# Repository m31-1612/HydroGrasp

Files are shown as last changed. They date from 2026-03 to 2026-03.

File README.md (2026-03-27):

# HydroGrasp

This is the official open-source repository for the paper:

**HydroGrasp: A Hydraulic Multi-Fingered Gripper**

📄 [Read the Paper](https://doi.org/10.1109/robio66223.2025.11377340)

---

## Hardware

### Manipulator

To manufacture a manipulator, you need to 3D print the following models in `CAD/Manipulator`. It is recommend to use resin (SLA) 3D printing to achieve better structural accuracy.

#### 3D Printing BOM

| Item | Quantity | Recommand Process|
|---|---|---|
|Base|1|SLA|
|EndNut|6|SLA / FDM|
|Link0|3|SLA|
|Link1|3|SLA|
|Link2|3|SLA|
|Sleeve1|3|SLA|
|Sleeve2|3|SLA|

To assemble these parts, you will also need the following components:

#### Component BOM

| Item | Specification | Quantity | Notes | Link |
|---|---|---|---|---|
| Dynamixel Servos | XL-330-M288-T | 3 | with cables & screws | https://en.robotis.com/shop_en/item.php?it_id=902-0163-000 |
| Shoulder Bolt | 4 × 22 × M3 | 3 | - | - |
| Shoulder Bolt | 4 × 35 × M3 | 12 | - | - |
| Lock Nut | M3 anti-slip | 15 | - | - |
| Heat-set Insert | M3 × 5 mm (height) × 3.5 mm (OD) | 6 | - | - |
| Push Rod | CJ1B4-15SU4 | 3 | - | https://e.tb.cn/h.iitMhi8EHR5U38x?tk=sMsP5Y1MS0p |
| Push Rod | CJ1B4-20SU4 | 3 | - | https://e.tb.cn/h.iitMhi8EHR5U38x?tk=sMsP5Y1MS0p |

### Assembly Instructions

1. Use a soldering iron to embed heat-set inserts into the EndNut.

2. For each of the CJ1B4-15SU4 push rod, remove the black nut at the front end. Pass the threaded portion that originally held the nut through Sleeve2, then reattach and tighten the black nut to secure it.

3. For each of the CJ1B4-20SU4 push rod, remove the black nut at the front end. Pass the threaded portion that originally held the nut through Sleeve1, then reattach and tighten the black nut to secure it.

4. Connect the threaded end of the push rod to the heat-set nut embedded in the EndNut.

5. Referring to the figures in the paper, use 4 × 35 shoulder bolts and lock nuts to connect three finger links and push rods, and adjust the screw tightness so that each joint rotates freely without resistance. Do not install the 4 × 22 screws at this stage.

6. Repeat the above steps three times to assemble three fingers.

7. Use the longer screws from the servo kit to secure the three servos to the base.

8. Attach Link0 of each finger to the servo horns using the longer screws provided in the Dynamixel kit.

9. Referring to the paper’s figures, install the shorter 4 × 22 shoulder bolts.

10. This base can be mounted, as needed, onto the end of xArm, Franka, or UR5. 

### Actuator

#### BOM

| Item | Specification | Quantity | Notes | Link |
|---|---|---|---|---|
| 3D Printed Parts | See `CAD/Actuator` | 1 set | Print each file once | - |
| Dynamixel Servos | XL-330-M288-T | 1 | with cables & screws | https://en.robotis.com/shop_en/item.php?it_id=902-0163-000 |
| syringe | 1mL | 1 | without needle | - |

### Assembly Instructions

1. Attach the gear to the servo horns using the longer screws provided in the Dynamixel kit.

2. Use the longer screws from the servo kit to secure the servo to the base.

3. Slide the rack into the groove of the base.

4. Insert the syringe plunger and handle into the grooves of the rack and the base, respectively.

### System Assembly

To build the complete system, you will need at least one manipulator and six actuators. In addition, the following materials are required.

| Item | Specification | Quantity | Notes |
|---|---|---|---|
| PVC tube | 4mm*2.5mm | as needed | - |
| T-type connectors | Suit for 4 mm tubing diameter | as needed | optional |

To drive each degree of freedom, connect PVC tube between the end of the push rod and the front end of the syringe. Then fill the closed cavity formed by the syringe, tubing, and push rod with purified water, ensuring that all air is removed. When the push rod is in the retracted state, the syringe plunger should be fully extended to achieve the maximum stroke.

In addition, you can use a T-type connector to assign two actuators to a single push rod, enabling hybrid control.

Finally, to drive the Dynamixel servos, you will need the following components. Please refer to the [official manual](https://emanual.robotis.com/docs/en/dxl/x/xl330-m288/) for proper connection and control of the servos.

| Item | Specification | Quantity | Link |
|---|---|---|---|
| U2D2 Hub | - | 1 | https://en.robotis.com/shop_en/item.php?it_id=902-0132-000 |
| U2D2 PHB Set | - | 1 | https://en.robotis.com/shop_en/item.php?it_id=902-0145-001 |
| DC Power Supply | 5V | 1 | - |

---

## Software

### Installation

The Dynamixel SDK can be installed using the following command:

```bash
pip install dynamixel_sdk
```

### Usage

Please refer to the [Official Dynamixel SDK Documentation](https://emanual.robotis.com/docs/en/software/dynamixel/dynamixel_sdk/download/) and our [paper](https://doi.org/10.1109/robio66223.2025.11377340) to implement the servo communication and actuation logic.

---

## Citation

If you use this repository in your research, please cite:

```bash
@INPROCEEDINGS{Zhang2025HydroGrasp,
  author={Zhang, Peiran and Tang, Ziyuan and Hu, Runze and Xiao, Chenxi},
  booktitle={2025 IEEE International Conference on Robotics and Biomimetics (ROBIO)}, 
  title={HydroGrasp: A Hydraulic Multi-Fingered Gripper}, 
  year={2025},
  volume={},
  number={},
  pages={442-447},
  doi={10.1109/ROBIO66223.2025.11377340}}
```

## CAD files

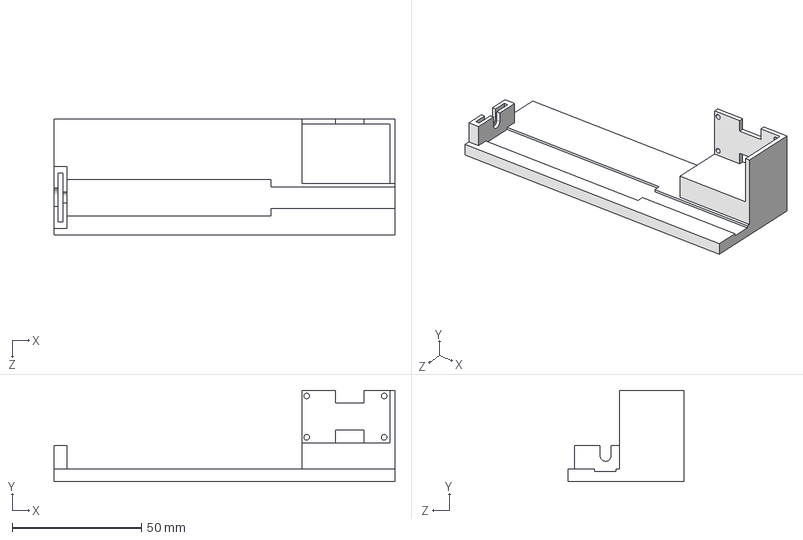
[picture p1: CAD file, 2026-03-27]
CAD/Actuator/Base.STEP
132.0 x 35.4 x 45.0 mm

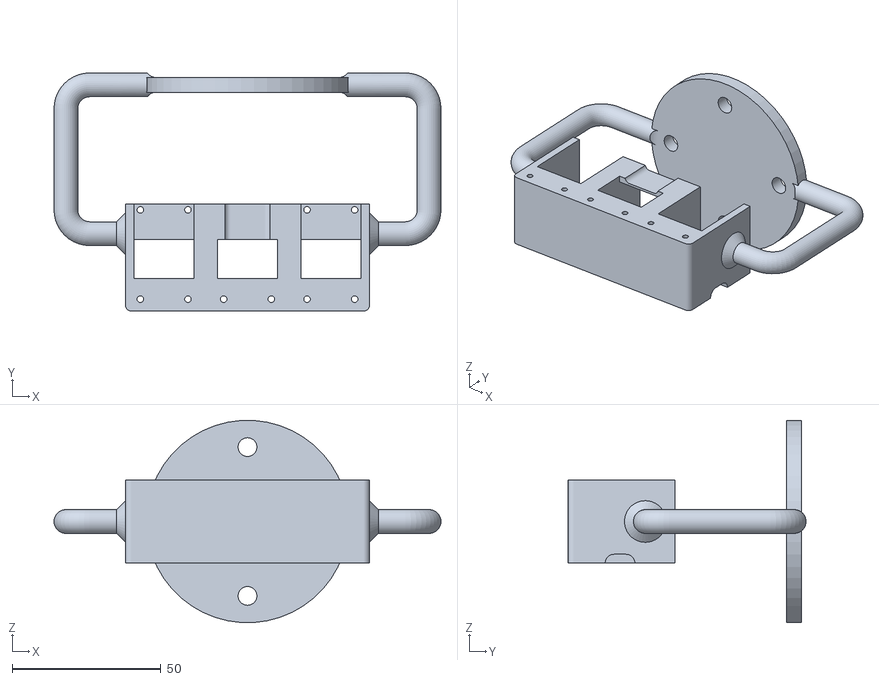
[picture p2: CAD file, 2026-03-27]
CAD/Manipulator/Base.STL
130.0 x 80.0 x 67.9

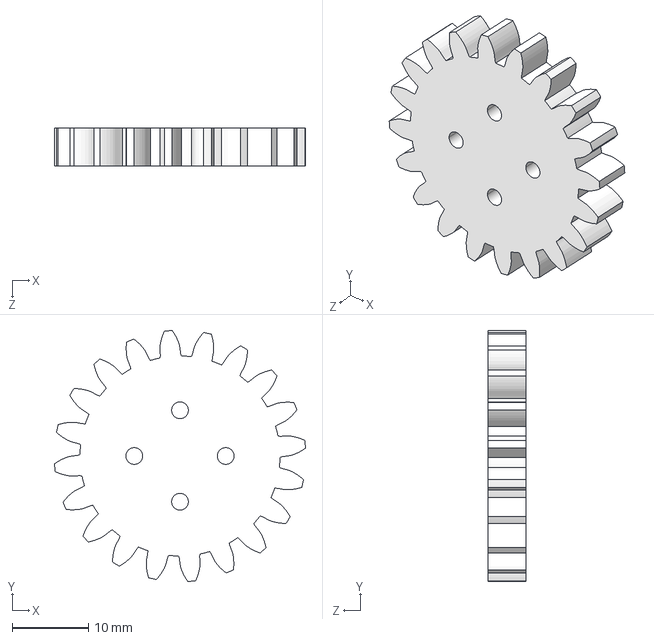
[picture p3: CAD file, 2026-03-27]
CAD/Actuator/Gear_M1.5_Z20.STEP
32.9 x 32.9 x 5.00 mm

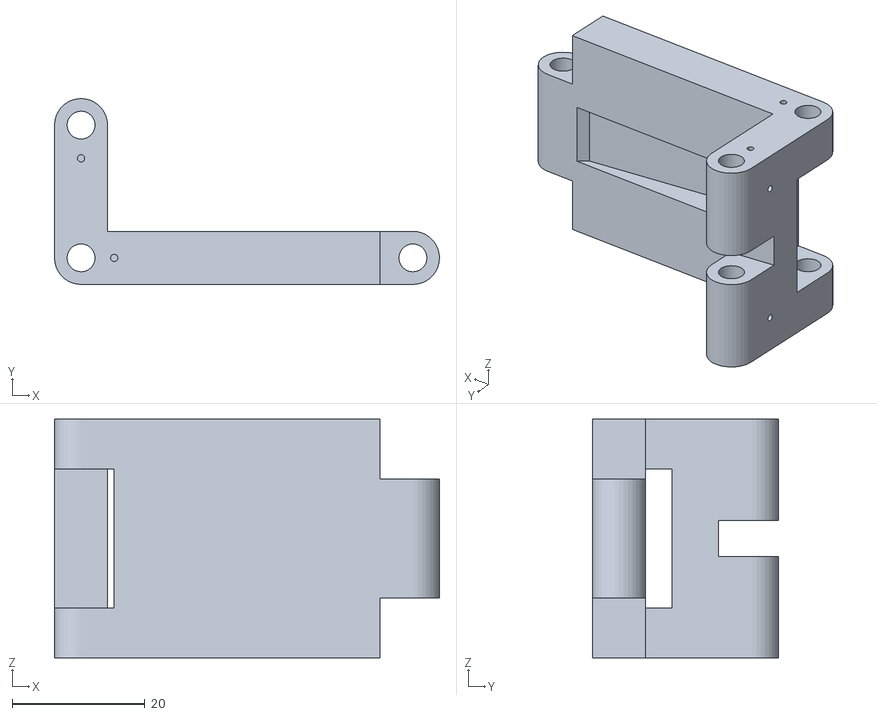
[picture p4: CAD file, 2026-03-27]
CAD/Manipulator/Link1.STL
58.0 x 28.0 x 36.0

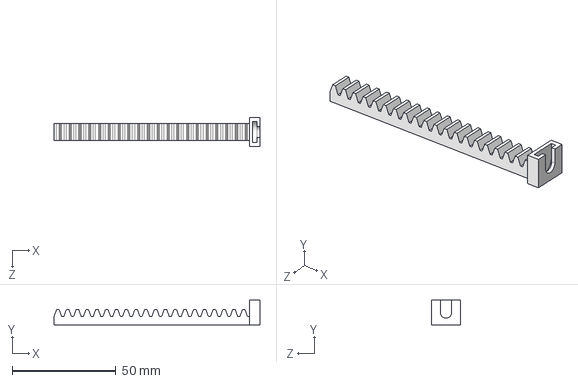
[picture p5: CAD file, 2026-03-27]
CAD/Actuator/Rack_M1.5_Z20.STEP
99.2 x 12.0 x 14.0 mm

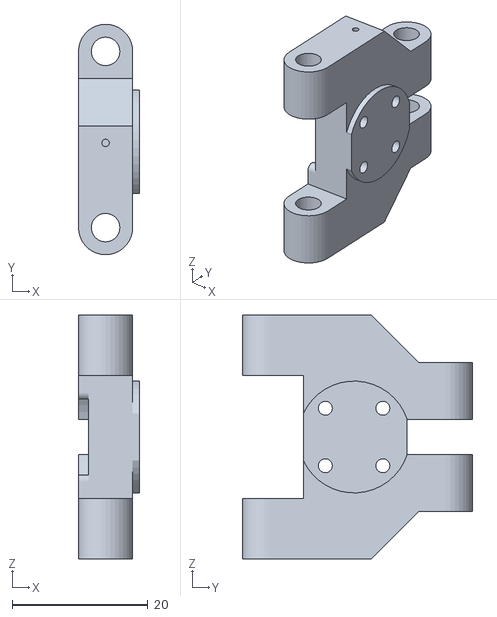
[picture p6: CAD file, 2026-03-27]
CAD/Manipulator/Link0.STL
9.00 x 34.0 x 36.0

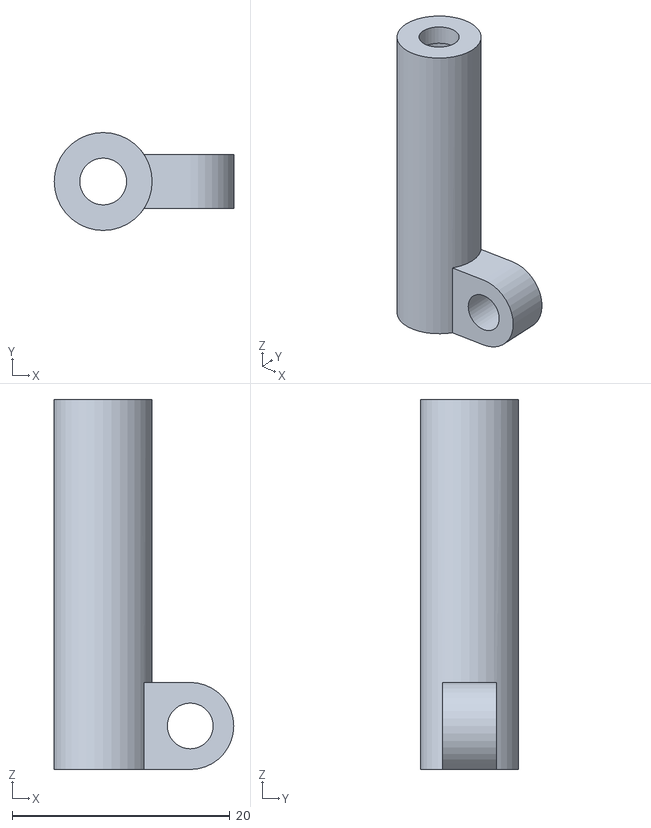
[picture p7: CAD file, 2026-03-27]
CAD/Manipulator/Sleeve2.STL
16.5 x 9.00 x 34.0

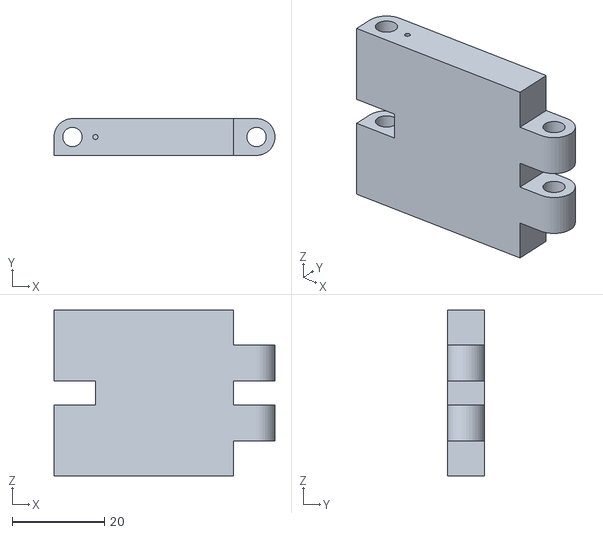
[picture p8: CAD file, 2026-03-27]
CAD/Manipulator/Link2.STL
48.0 x 8.00 x 36.0

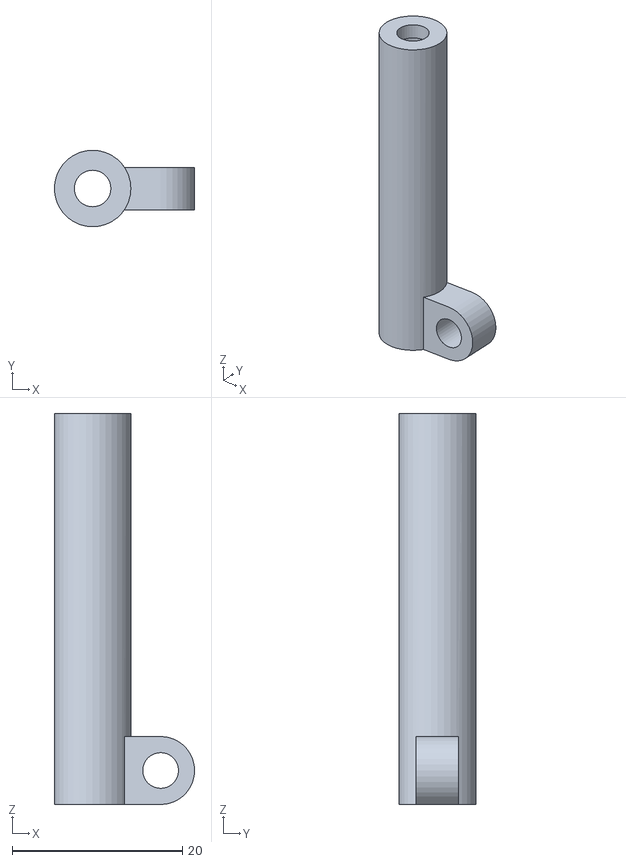
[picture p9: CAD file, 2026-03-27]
CAD/Manipulator/Sleeve1.STL
16.5 x 9.00 x 46.0

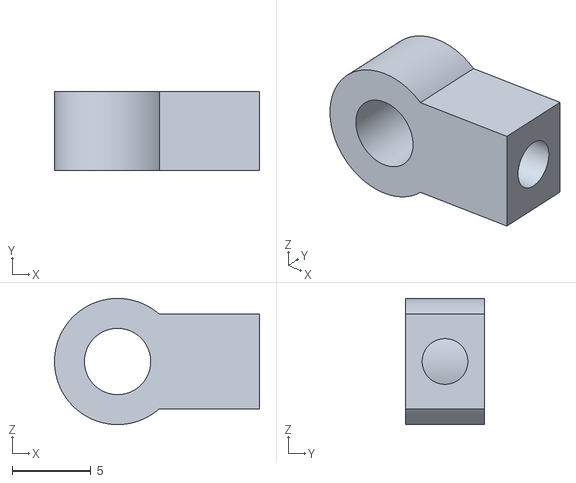
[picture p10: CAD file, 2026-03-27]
CAD/Manipulator/EndNut.STL
13.0 x 5.00 x 8.00
